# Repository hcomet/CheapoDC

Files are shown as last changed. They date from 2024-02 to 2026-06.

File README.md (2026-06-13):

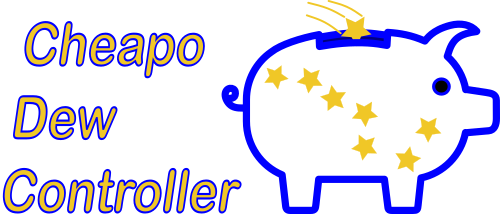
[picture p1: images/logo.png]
CheapoDC Logo
# 

# Introducing CheapoDC

The Cheapo Dew Controller, or CheapoDC, is a low cost, easy to build DIY dew controller based on an ESP32-C3 mini.
Parts required include the ESP32-C3 mini, a MOSFET module for each output, a 12V to 5V buck converter, some protoboard,
 RCA sockets, a 12V barrel socket and wire. Cost of the parts should be less than $20 for a unit that
controls 2 dew heater straps.

A primary goal was to keep the project cheap, simple and easy with:

* minimal low cost off the shelf components
* no coding or Arduino IDE experience necessary with both [WebFlash](https://hcomet.github.io/CheapoDC/CheapoDCFlash.html) and [HTTP OTA Update](https://hcomet.github.io/CheapoDC/CheapoDCWebUpdate.html) support
* Comprehensive [Web UI](#web-ui) for configuration and management
* [INDI](https://www.indilib.org/) and [StellarMate](https://stellarmate.com/) support 'out-of-the-box'

CheapoDC can select from four weather sources to provide the local temperature and humidity. 
* The first two, **OpenWeather** and **Open-Meteo**, leverage the ESP32 WiFi
capability to query one of the two open weather service APIs. Either the [OpenWeather](https://openweathermap.org/) API
or the [Open-Meteo](https://open-meteo.com/) API may be used to retrieve ambient temperature, humidity and dew point
for the controller's geographic location. No additional
components, such as temperature or humidity probes, are required with these weather sources. 
* The third weather source option, **External Source**, allows weather information to be pushed to the CheapoDC via the API. A personal weather station may be leveraged for local weather data using this option.
* The fourth option, **Internal Source**, requires an optional Humidity Sensor be added to the CheapoDC to provide required weather data.

The CheapoDC may be set up using a basic configuration with two dew strap outputs or it may be configured with up to
four additional outputs or the optional humidity sensor. Each CheapoDC Output is controlled by a separate MOSFET module tied to one of the ESP32
GPIO pins. The four additional outputs may be configured to be managed either automatically using the CheapoDC dew
control algorithm, along with the two main dew controller outputs,
or manually via the Web UI or API. Dew control algorithm managed pins and thus dew strap outputs are all tied to the
same ESP32 PWM channel and will have the same output.

CheapoDC hardware details can be found in the [Hardware](#hardware) section of this document.

CheapoDC firmware installation details may be found with the source code in the [CheapoDC/README.md](./CheapoDC/README.md#installing-cheapodc). Installation may be done by:

* Using WebFlash, a web-based utility that allows for the installation of the latest firmware directly to your ESP32-C3 based device.
* Building it yourself with the Arduino IDE.

CheapoDC also supports web-based Over-the-air (OTA) upgrades of the firmware using the CheapoDC Web UI.

# How the Dew Control Algorithm Works

When working in Automated mode, the controller will periodically calculate the power output to the dew straps using the
calculations below. The default output calculation or update period is 1 minute.

## Controller Power Output Calculation

### Variables

* **Set Point** = ***SP***
  * as set using the **Set Point Mode** selection.
* **Reference Temperature** = ***RT***
  * as set using the **Temperature Mode** selection.
* **Track Point** = ***TP***
  * the calculated temperature point where the **Tracking Range** starts. A **Reference Temperature** less than or equal
to the **Track Point** will cause the controller to use **Maximum Output**.
* **Track Point Offset** = ***TPO***
  * a temperature offset applied to the **Set Point** when calculating the **Track Point** relative to the **Set Point**.
The **Track Point Offset** may be set from -5.0&deg;C to 5.0&deg;C. The default is 0.0&deg;C.
* **Tracking Range** = ***TR***
  * the temperature range starting at the **Track Point** where the controller output ramps up from **Minimum Output** at the high end of the range to **Maximum Output** at the low end of the range. The range may be set to values from 4.0&deg;C to 10.0&deg;C. The default is 4.0&deg;C.
* **Power Output** = ***PO***
  * the percentage of power the controller is outputting to the dew straps. It varies from the **Minimum Output** setting to the **Maximum Output** setting.
* **Minimum Output** = ***MinO***
  * the minimum percent power setting for the controller to output when not in the **Off** **Controller Mode**. Defaults to 0%.
* **Maximum Output** = ***MaxO***
  * the maximum percent power setting for the controller to output when at full output. Defaults to 100%.

### Calculations

$`TP = SP + TPO`$

$`IF`$ $`(RT <= TP )`$ $`THEN`$ $`PO= MaxO`$

$`IF`$ $`(RT >= (TP + TR))`$ $`THEN`$ $`PO = MinO`$

$`IF`$ $`(RT <(TP + TR))`$ $`THEN`$ $`PO = MinO + (MaxO - MinO) * ( 1 - ((RT - TP)/TR))`$

### Examples

Example 1 is primarily a reference image to illustrate the variables defined above.

* Power Output curve is shown relative to the Track Point and the Tracking Range. While the Reference Temperature is greater than the high end of the Tracking Range the Power Output is set to Minimum Output. The Power Output ramps up linearly through the Tracking Range from the Minimum Output to the Maximum Output as the Reference Temperature drops.
* This example shows a Reference Temperature, RT = 8°C, which is greater than the upper end of the Tracking Range, causing Power Output to be set to Minimum Output. In this case Minimum Output is set to 10%.
* The upper end of the Tracking Range, at 7°C, is determined from the Set Point (SP = -2°C) plus the Track Point Offset (TPO = 4°C), creating a Tack Point, TP = 2°C, plus the Tracking Range (TR = 5°C).  

   **NOTE:** The Set Point and the Reference Temperature values may vary from one output calculation to the next with each weather update.

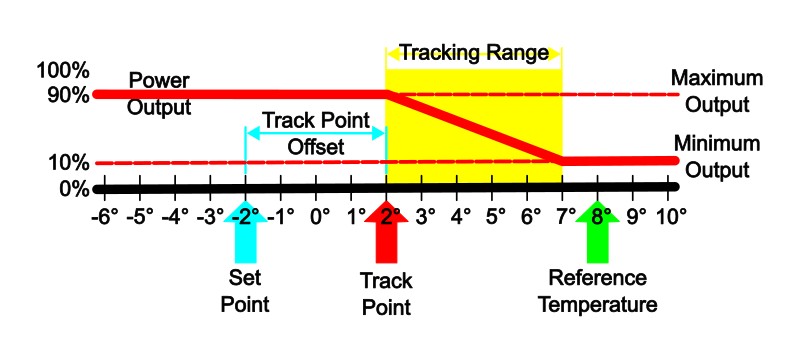
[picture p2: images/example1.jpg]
Example 1


Example 2 shows changing the values of the controller configuration variables can affect the Power Output calculation.

* The Set Point, SP = -2°C, and the Reference Temperature, RT = 8°C, the same as in Example 1. However, changing the Track Point Offset, now TPO = 2°C, and the Tracking Range, now TR = 10°C, has changed the Power Output as well as flattening the Power Output curve.
* The Maximum Output has been increased, MaxO = 100%, to allow full power output to be reached at 0&deg;C.

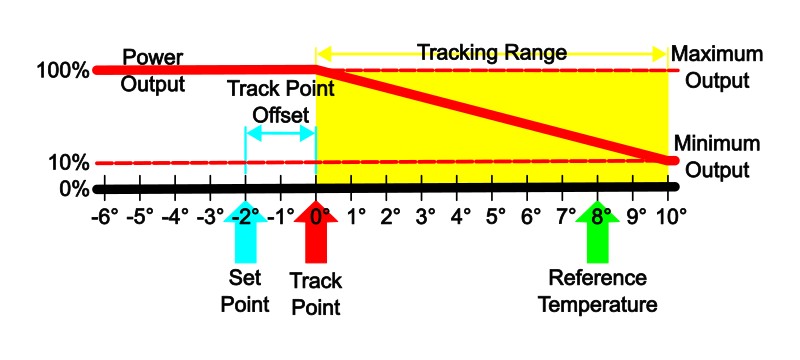
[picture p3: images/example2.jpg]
Example 2


## Dew Controller Configuration Settings

The following modes of operation are used by CheapoDC to determine overall controller operation as well as which values to assign to the Set Point and Reference Temperature when calculating output.

### Controller Mode

The Controller Mode selects the overall operating mode of the dew controller.

#### Automatic

* Uses the **Set Point Mode** and **Temperature Mode** settings to calculate the controller output based on the Power Output calculations above. In Automatic mode the Power Output calculation will be run periodically based on the Update Output Every setting. This may be set to a value from 1 to 20 minutes. The default is 1 minute. Automatic mode may be used with or without internet access.

#### Manual

* Controller output is manually controlled by setting the **Dew Controller Output** either through the Web UI or the API. When in Manual mode the periodic Power Output calculation is suspended. Using Manual control is an option if internet access for OpenWeather API queries is not available.

#### Off

* Controller output is set to Zero.

### Set Point Mode

The Set Point Mode selects what will be used as the SetPoint for calculating Power Output.

#### Dew Point

* Uses the **Dew Point** as the Set Point used for calculating output. This is the default selection.

#### Temperature

* Uses a **Temperature Set Point** value input via the Web UI or API as the Set Point for calculating output. If the CheapoDC is being used without internet access, then this mode allows a Set Point to be defined when the Dew Point cannot be determined through the OpenWeather API.

#### Midpoint

* Uses the midpoint between the current **Temperature Mode** temperature value and the Dew Point value as the Set Point for calculating output. The impact of selecting this mode is to effectively double the Tracking Range and further flatten the ramp of the Power Output curve.

### Temperature Mode

The Temperature Mode selects how the Reference Temperature will be determined for calculating the Power Output.

#### Weather Source

* Uses the Ambient Temperature returned by the selected Weather Source. This is then used as the Reference Temperature for calculating the controller output.

#### External Input

* Use the **External Input** temperature set through the [Web UI](#cheapodc-controller-configuration) or [API](#cheapodc-api) as the reference temperature for calculating the controller output. This may be the preferred mode when using the controller with KStars/Indi. The CheapoDC [Indilib driver](#indi-driver) can use a temperature probe attached to a focuser as the external input.  
<br>**NOTE:** If no temperature values have been set for External Input, then a value of **-127.0°C** will be shown. The Controller, when in Automatic Mode with Temperature Mode set to External Input,  will set output power at the configured minimum output until a value is set via the WebUI or API.

## Hardware

One of the goals with the CheapoDC is for it to be relatively easy to assemble. Although some soldering will be
required the number of connections is minimized by using common modules. This section focuses on what is required
to build a basic two dew strap controller commonly needed for a primary telescope and secondary guide scope.

If you need additional dew controller outputs or the ability remotely control the power to another device then that
information is covered [here](https://hcomet.github.io/CheapoDC/CheapoDCBuild.html).

If you are looking to add the optional SHT30 Humidity sensor to support a complete standalone device, that information is covered [here](https://hcomet.github.io/CheapoDC/CheapoDCSensor.html).

### Component list

* ESP32-C3 SuperMini (Other ESP32 modules should work but this one is very small and low priced) Example: [https://www.aliexpress.com/item/1005005967641936.html?spm=a2g0o.order_list.order_list_main.10.3b2c1802dRy3Tw](https://www.aliexpress.com/item/1005005967641936.html?spm=a2g0o.order_list.order_list_main.10.3b2c1802dRy3Tw)
* Buck converter to reduce 12V to 5V. I used an [LM2596 Module](https://www.amazon.ca/dp/B08Q2YKJ6Q?psc=1&ref=ppx_yo2ov_dt_b_product_details). You could also use an [MP1584EN Module](https://www.amazon.ca/eBoot-MP1584EN-Converter-Adjustable-Module/dp/B01MQGMOKI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). These modules often have an adjustable output. You'll need to use a Voltmeter to adjust the output to 5 volts before hooking it up.
* Two [dual-MOSFET Modules](https://www.amazon.ca/dp/B08ZNDG6RY?psc=1&ref=ppx_yo2ov_dt_b_product_details) to handle output to the dew straps while being able to be triggered by the 3.3V levels from the ESP32 PWM pins.
* A resettable fuse that can handle 5A. An example [5A PPTC](https://www.amazon.ca/10pcs-5000MA-Resettable-RGEF500-GF500/dp/B092T9Q3QR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)
* Optionally an LED and resistor for the status LED. Many astrophotographers do not want power LEDs or lights of any sort on their equipment. If you fall into this category, then just use the ESP32 onboard LED as the status LED. If you would prefer a visible status LED on your project case, then you may optionally add one. Status LED details may be found in the [Status LED Section](#cheapodc-status-led).  
In my implementation I used a red LED connected to the same pin as the onboard LED, pin 8. I used a 1K resistor to keep the LED fairly dim while still working.
* Some assorted hardware:
  * 12VDC 5.5mm x 2.1mm socket. Common socket size used for Astronomy.
  * Switch that will work for 12VDC at 5A.
  * Two RCA sockets. RCA plugs are commonly used for dew straps.

### Basic Wiring Diagram

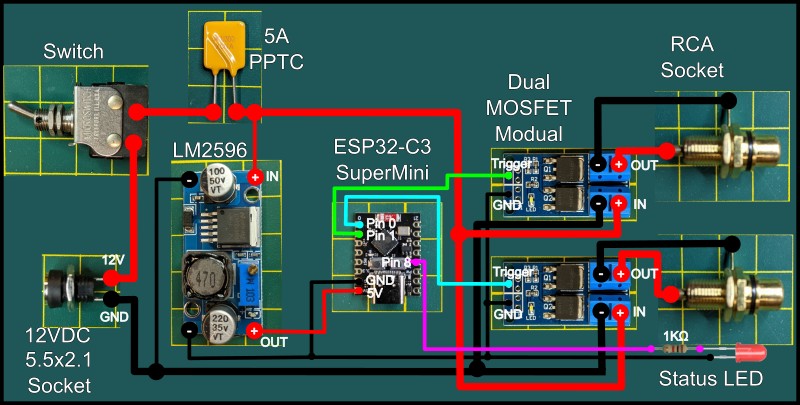
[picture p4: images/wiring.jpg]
Wiring Diagram


The default configuration for the basic dual output controller uses Controller Outputs, 0 and 1, mapped to GPIO pins 0 and 1.
If you cannot use these GPIO pins, then they may be changed using the Web UI on the [Device Management](#cheapodc-device-management)
page or the default values may be changed in the [CDCDefines.h](CheapoDC/README.md#configure-firmware-in-the-cdcdefinesh-file) file
before building the firmware.

### Working Implementation

Assembled in a 6 inch piece of 2"x1" aluminum channel. This also has Pin 8, which is the status LED, connected to an extra LED on the left side for external visibility. The ESP32-C3 is also mounted in some protoboard to make the wiring easier. If you plan to use a small case like this, use silicone hookup wire. The extra flexibility of silicone wire will save a lot of frustration. I used 22 awg wire for the 5V and 3.3V ESP32 connections and 18 awg wire for the 12V connections.

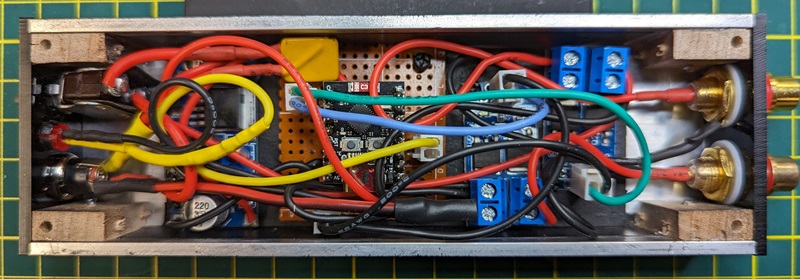
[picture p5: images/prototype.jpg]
Working Prototype


Two completed CheapoDCs from the outside.

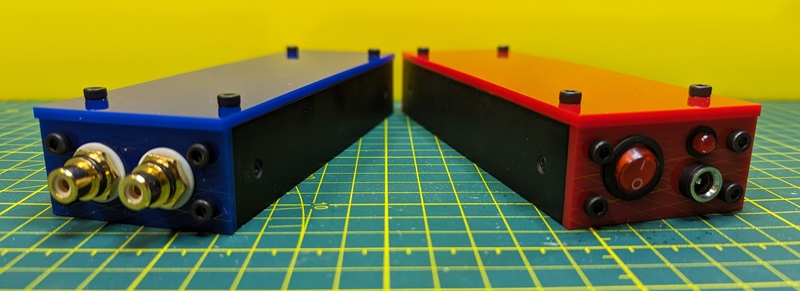
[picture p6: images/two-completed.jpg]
Two completed


## Firmware

How to build the CheapoDC firmware can be found [here](/CheapoDC/README.md). All aspects of the CheapoDC are configurable through the [WebUI](#web-ui) making [WebFlash](https://hcomet.github.io/CheapoDC/CheapoDCFlash.html) the easiest way to install and then configure firmware.

## Weather Source

CheapoDC requires temperature and humidity information to calculate the dew point and then the required controller output power for dew prevention. This information is provided by a Weather Source. CheapoDC can query one of two open weather API services, be provided weather information via the CheapoDC API or use an optional internal humidity sensor. The Weather Source may be set using the [Web UI](#cheapodc-controller-configuration) or through the [API](#cheapodc-api). The following four Weather Sources are available:

### [Open-Meteo](https://open-meteo.com/) (Default)

pen-Meteo, an open API based weather service, is the default Weather Source for CheapoDC. Use of the Open-Meteo API does not require any registration for current weather queries. The free level allows for 10,000 API calls per day. Weather updates seem to be regular at a 15 minute interval. While using a 5 minute query interval, several CheapoDCs can be running at the same time without issue. Requires correct location information and internet access to work.

### [OpenWeather](https://openweathermap.org/)

 OpenWeather, also an API based weather service, requires a registered account and API key. The account is free and allows for up to 60 queries/minute and 1,000,000 per month. Weather updates can occur from 5 to 20 minutes apart. Doing an API call every 5 minutes is more than adequate for dew control and even with 2 or 3 CheapoDC's sharing a key should have no issue at the free account level. Register and get your API key [here](https://home.openweathermap.org/users/sign_up). Requires correct location information and internet access to work.

### External Source

 When the Weather Source is set to External Source the temperature and humidity values for your location must be set via the CheapoDC API. This allows for integration with other weather services or personal weather stations. The [INDI driver](#indi-driver) supports this capability.

 ### Internal Source

 When the Weather Source is set to Internal Source the temperature and humidity values for your location are retrieved from an SHT3x series humidity sensor. The sensor must be connected to the ESP32 C3 and configured on the [Device Management](#cheapodc-device-management) page of the WebUI.

### Which Open Weather Service to use?

Both services require a location using Latitude and Longitude which you can set using the CheapoDC [Web UI](/README.md#web-ui) or [CheapoDC API](#cheapodc-api). Both sources will use weather stations close to the provided coordinates. OpenWeather provides the name of the weather station used in its response. Open-Meteo does not. If run side-by-side with the same co-ordinates they provide slightly different results. You may want to check which service provides the best results for your location.

As indicated the default service is Open-Meteo. This is primarily because no registration is required to use the open service.

## Web UI

CheapoDC comes with a Web UI that supports basic web authentication. The default is "admin" for both username and password. The password can (and should) be changed on the WebUI [Device Management](#cheapodc-device-management) page. TLS (or HTTPS) is not supported. Security is minimal with the intention to provide a deterrent to someone easily doing an OTA upgrade to the firmware or uploading files to the LittleFS partition.

The Web UI has 4 main pages, a dashboard, a configuration page, a device management page and a file management page.

### CheapoDC Dashboard

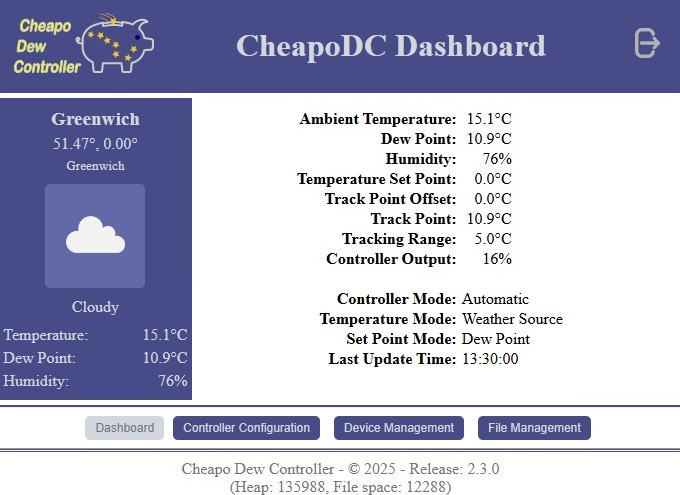
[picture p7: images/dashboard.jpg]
CheapoDC Dashboard
  

The Dashboard provides a summary of the current location, weather, controller output and settings. Internet connectivity is required for current weather information and the weather icon.

### CheapoDC Controller Configuration

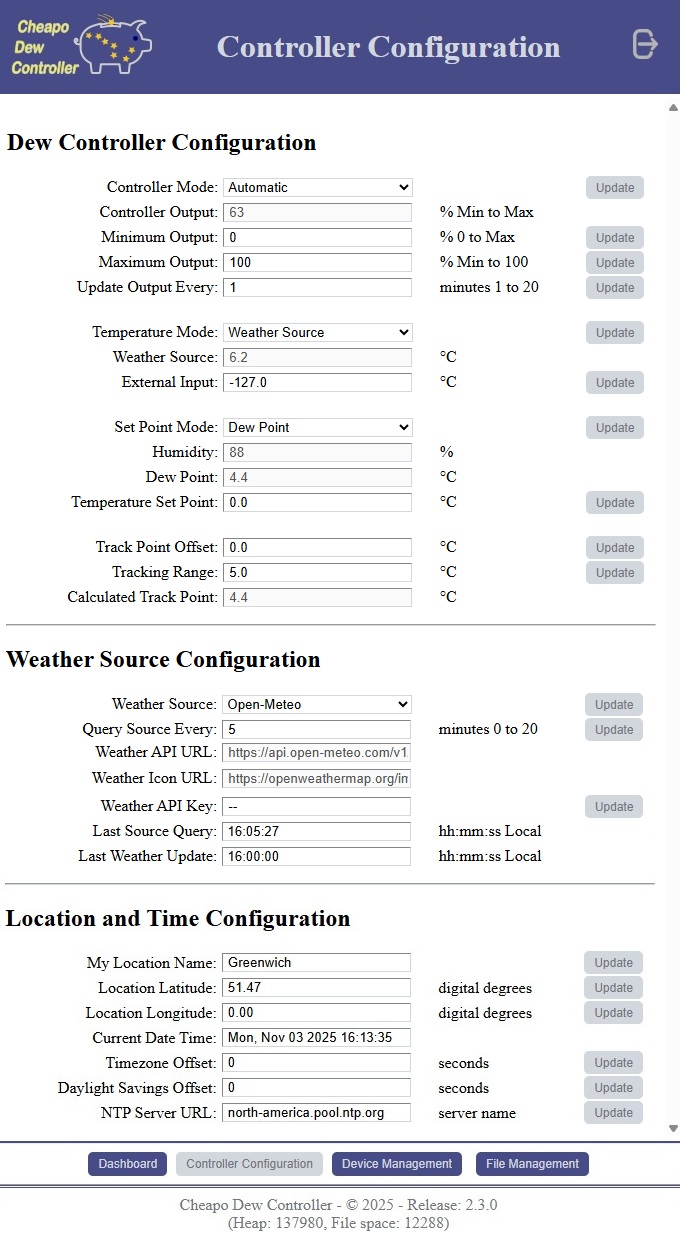
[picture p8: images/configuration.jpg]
CheapoDC Configuration
  

CheapoDC Configuration page is where dew controller parameters may be set. These include the [Controller Mode](#controller-mode), [Temperature Mode](#temperature-mode), [Set Point Mode](#set-point-mode), [Weather Source](#weather-source-1) and [variables](#variables) that affect dew controller output.

The Location and Time Zone may be set here and are required for proper operation when using either Open-Meteo or OpenWeather as a Weather Source.

### CheapoDC Device Management

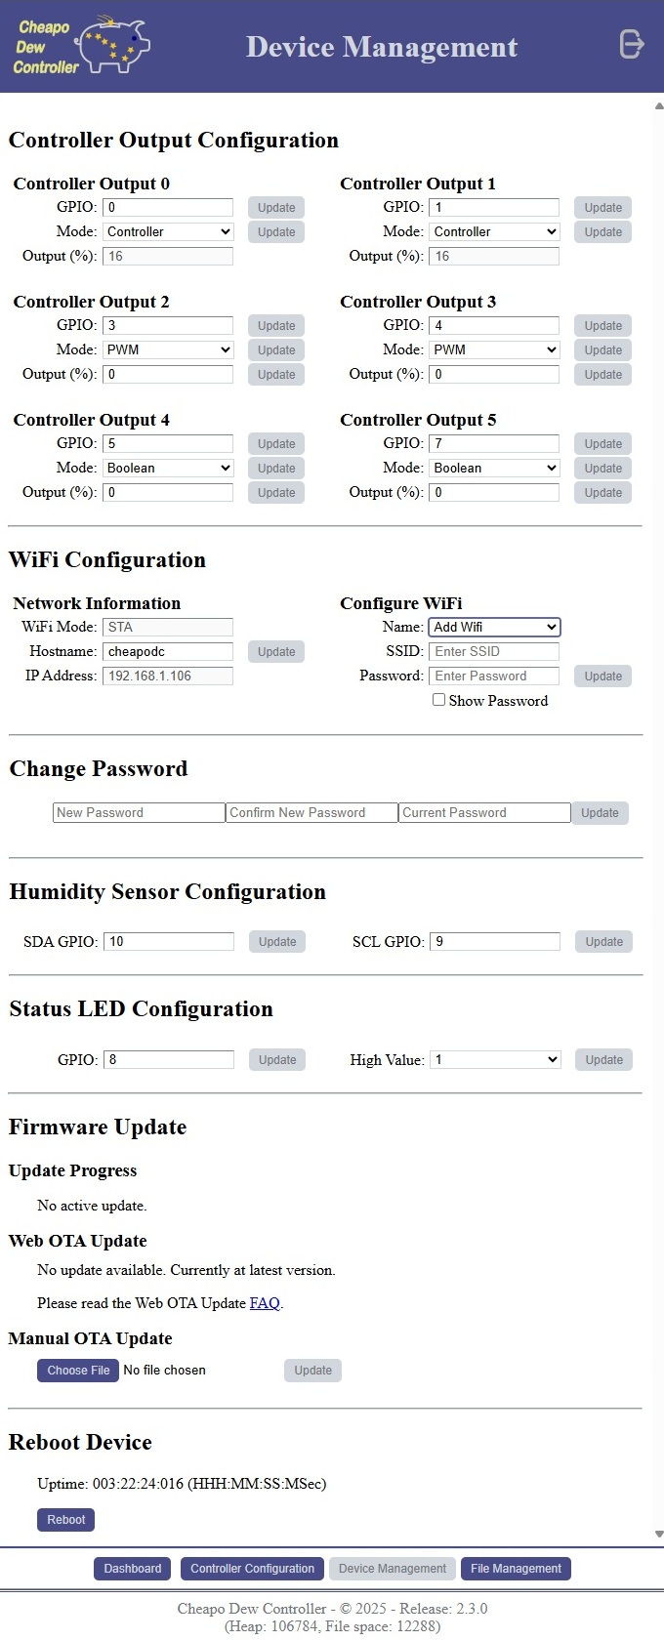
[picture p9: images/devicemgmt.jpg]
CheapoDC Device Management
  

The Device Management page is where device level configuration is done for the CheapoDC. This includes:

#### Controller Output Configuration

Used to configure GPIO Pin mappings for outputs as well as setting the Output Mode for each output. The CheapoDC can support up to 6 Controller Output Pins, Pin 0 through Pin 5. Pins 0 and 1 may only be used as dew controller outputs while Pins 2 through 5 may be set to any of the supported Output Modes:

##### Output Modes

|Output Mode|Description|Supported Output Pins|
|---|---|---|
|Disabled|Output is disabled. The default. GPIO pin mapping set to -1.|Pin 0 through Pin 5|
|Controller|Output is controlled by the dew controller.|Pin 0 through Pin 5|
|PWM|Output is manually controlled using PWM and output may be set from 0% to 100%.|Pin 2 through Pin 5|
|Boolean|Output is manually controlled and may be either Off (0%) or On (100%).|Pin 2 through Pin 5|

Note that a Controller Output Pin to GPIO Pin mapping must be set before an Output Mode may be selected. These settings may be controlled via the Web UI or the API.

#### WiFi Configuration

Shows current network information and allows you to configure the hostname and WiFi access point to use for network access. CheapoDC can be configured to step through multiple access points to make a WiFi connection.

* Network Information
  * WiFi Mode: STA = Station Mode, AP = Access Point Mode.
  * Hostname: Current active hostname. If updated a reboot is required to see the new hostname.  
  **Note:** Changing the hostname will also change the SSID for the device when in Access Point Mode.
  * IP Address.
* Configure WiFi
  * Name: Allows you to pick an access point for editing the password. Or select `Add WiFi` to add an access point.
  * SSID: Is the access point SSID point to add or edit. To delete an access point, blank out the SSID and click **Update**.
  * Password: Is the password for the access point. **Show Password** will only work for adding a new WiFi access point.

Changes to any of the WiFi Configuration setting require a reboot to take effect.

#### Change Password

Changing the default password of ***admin*** to your own password is recommended.

#### Humidity Sensor Configuration

Used to configure which pins are used for by the SHT3x humidity sensor. The humidity sensor uses the I2C protocol and two GPIO pins are required. One for the I2C SDA (data) line and one for the I2C SCL (clock) line. If using the humidity sensor, then it's recommended to use pin 10 for SDA GPIO and pin 9 for SCL GPIO. If not using the humidity sensor, then leave the two values set to -1. If either setting has a negative value, then the firmware will not attempt to initialize I2C and the humidity sensor.

#### Status LED Configuration

Used to change the Status LED pin mapping from the default of GPIO 8. Also used to set the active High Value to ***1*** or ***0***.

#### Firmware Update

CheapoDC supports two methods for updating firmware.

1. Web OTA Update: Will indicate when a new release is available and then allow for an HTTP based OTA update. This will update both the firmware and data partitions while preserving your configuration settings. No software or Arduino IDE knowledge is required for this update method. Please consult the [Web OTA Update FAQ](https://hcomet.github.io/CheapoDC/CheapoDCWebUpdate.html) for details.
2. Manual OTA Update: Allows for an OTA update to firmware that has been compiled and built on your own machine. This only updates the data partition. You will need to manually update the files in the data partition using the [File Management UI](#cheapodc-file-management). At least Arduino IDE knowledge is required for this method.

#### Reboot Device

To remotely reboot the CheapoDC.

### CheapoDC File Management

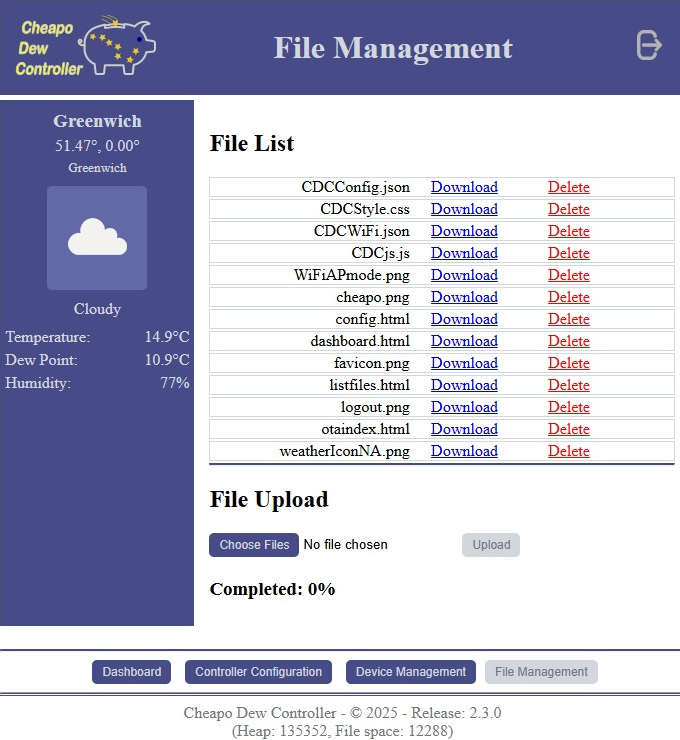
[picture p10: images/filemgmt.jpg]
  

The CheapoDC uses LittleFS for file storage on the ESP32. Although LittleFS supports directories as well as files CheapoDC uses a flat structure and all files are managed at the root. The file management page supports upload, download and delete functions.

## CheapoDC Status LED

The Status LED is used to provide information about the current status of the CheapoDC. Status blinking lasts for 10 seconds. It will blink as WiFi access attempts are made. If a Station mode connection is successfully made to an access point, then the status LED will slow blink (1 second cycle). If no connection is made, then the CheapoDC will go into Access Point mode. The status LED will then fast blink (200ms cycle).

The status LED will also blink for 10 seconds after the controller changes the power output and after an API or Web UI driven controller configuration change.

If the status LED is not turning off after connecting to WiFI or after the 10 second blink, then you may need to reverse the High value setting. This can also be done in the Web UI by changing the High Value setting in [Status LED Configuration](#status-led-configuration).

## CheapoDC API

The CheapoDC provides API access to all configuration and data items available through the [Web UI](/README.md#web-ui). There is no authentication support in the API, but the API also does not support firmware OTA updates or file management. These can only be done through the Web UI.

CheapoDC supports two API mechanisms:

1. TCP API using JSON syntax
2. Basic Web API utilizing HTTP POST

The APIs use the same commands which are listed in the top of [CDCommands.cpp](/CheapoDC/CDCommands.cpp). Commands are 2 to 4 character strings. For each command there is a map indicating:

* the number of the command,
* whether or not the value associated with the command is to be saved or loaded using the CDCConfig.json file,
* units used for the value. Units are HTML or JSON formatted and may be:
  * None: empty string.
  * Degrees Celsius: "\&deg;C"
  * Decimal Degrees: "\&deg;"
  * Percent: "\&percnt;"
  * Milliseconds: "msec"
  * Seconds: "sec"
  * Minutes: "min"
  * JSON ENUM, for enumerated values like Controller Mode.
    * ie: "{"Mode":["Automatic","Manual","Off"]}"

The table below provides a list of the commands, but the code is the final correct source of truth here.

* String maximum lengths are identified in the table.
* Floats are truncated to 2 decimal places.
* All commands except **QN** and **PWDH** support getter API methods.
* For security reasons, **PWDH** does not allow a getter API but it also restricts the setter to the Web API and HTTP POST method. It also requires that the current Password digest hash be submitted as a second parameter.
* The **QN** command is a setter only command. It requires a value that is not Null. "NA" works.
* Commands supporting a **Setter** method are identified.
* The **ATPQ** and **HU** commands are only setter commands when Weather Source is set to External Source.
* Date and time responses are in local time based on the Time Zone Offset and DST Offset values.
* Controller Output commands: CPP#, CPM# and CPO# are independent API commands where the # must be one of 0, 1, 2, 3, 4 or 5.
* Controller Output command CPP# allows a Controller Output to be mapped to -1 for Disabled or GPIO 0 through 39. Which actual GPIO pin to choose is ESP32 module dependent.
* Using an invalid command or trying a setter on a command not supporting a setter will return an error.
* Strictly speaking command values are always treated as Strings since the values are always enclosed in quotes in the JSON. Conversion to appropriate type is handled internally.
* The **CLC** command has been deprecated.

### CheapoDC Commands

|Command|Setter|Units|Type|Description|
|:---:|:---:|-----|----|---|
| TMFL |&cross;|  HTML | String [*] | File list in HTML for use in Web UI |
| WICON  |&cross;|  None | String [4] | Weather Icon for use with OpenWeather |
| WDESC  |&cross;|  None | String [32]| Weather description |
| ATPQ |&check;|  &deg;C | Float | Ambient temperature from weather query<br>Settable when Weather Source is set to External Source |
| HU |&check;|  &percnt; | Integer | Relative humidity (0 to 100)<br>Settable when Weather Source is set to External Source. |
| DP |&cross;|  &deg;C | Float | Dew point|
| SP |&check;|  &deg;C | Float | Temperature set point|
| TPO |&check;|  &deg;C | Float | Track Point offset (-5.0 to 5.0)|
| TKR |&check;|  &deg;C | Float | Tracking range (4.0 to 10.0)|
| DCO |&check;|  &percnt; | Float | Dew Controller Output (0 to 100)<br>Settable when Dew Controller Mode set to Manual. |
| WS |&check;|  None | ENUM | Weather source <br>Open-Meteo = 0<br>OpenWeather = 1<br>External Source = 2<br>Internal Source = 3|
| LQT |&cross;|  None | String [32] | Last weather query time|
| LQD |&cross;|  None | String [32] | Last weather query date|
| QN |&check;|  None | String [4] | Query weather now (Set only command)|
| FW |&cross;|  None | String [16] | firmware version|
| HP |&cross;|  Bytes | Integer | Heap size|
| LFS |&cross;|  Bytes | Integer | LittleFS remaining space|
| DCM |&check;| Enum | Enum | Dew controller mode<br>Automatic = 0<br>Manual = 1<br>Off = 2|
| DCTM |&check;| Enum | Enum | Dew controller temperature mode<br>Weather Source = 0<br>External Input = 1 |
| SPM |&check;| Enum | Enum | Dew controller set point mode<br>Dew Point = 0<br>Temperature = 1<br>Midpoint = 2 |
| WQE |&check;|  Minutes | Integer | Weather query every|
| UOE |&check;|  Minutes | Integer | update output every|
| WAPI |&cross;|  None | String [256] | Weather API URL|
| WIURL  |&cross;|  None | String [256] | Weather Icon URL|
| WKEY |&check;|  None | String [64] | Weather API Key|
| LAT |&check;|  &deg; (Digital) | Float | Location latitude (-90.00 to 90.00)|
| LON |&check;|  &deg; (Digital) | Float | Location longitude (-180.00 to 180.00)|
| LNM |&check;|  None | String [32] | Location name|
| TMZ |&check;|  Seconds | Integer | Location time zone (seconds)|
| DST |&check;|  Seconds | Integer | Location DST offset (seconds)|
| LED |&check;|  None | Integer | Status LED GPIO pin|
|LEDH|&check;|None|Integer|Status LED High value.<br>1 or 0.|
| NTP |&check;|  None | String [64] | NTP serverName|
| OMIN |&check;|  &percnt; | Integer | DC Min output (0 to Max-1)|
| OMAX |&check;|  &percnt; | Integer | DC Max output (Min+1 to 100)|
| CDT |&cross;|  None | String [64] | Current Date Time|
| ATPX |&check;|  &deg;C | Float | External Temperature input by external app|
| CTP |&cross;|  &deg;C | Float | Current Track Point Temperature|
| WUL |&cross;|  None | String [32] | Weather station reported in query|
|  ~~CLC~~ |&cross;|  &percnt; | ~~Integer~~ | ***Deprecated***|
| LWUT |&cross;| None | String [32] | Last weather update time<br>hh:mm:ss|
| LWUD |&cross;|  None  | String [32] | Last weather update date<br>DDD, dd MMM yyyy|
| UPT |&cross;|  None | Integer | Device uptime<br>hhh:mm:ss:msec|
| WIFI |&cross;|  None | String [4] | WIFI mode AP (Access Point) or STA (Station Mode)|
| IP |&cross;|  None | String [16] | IP Address|
| HN |&cross;|  None | String [16] | Host name |
| WQEN |&check;|  None | Bool | Web Query Enabled<br>False = 0<br>True = 1|
| CPP# |&check;|  None | Integer |Controller Output (0 to 5) to GPIO pin mapping<br>-1 to 39<br>-1 = Disabled|
| CPM# |&check;|  None | ENUM |Controller Output (2 to 5) Mode <br>Disabled = 0<br>Controller = 1<br>PWM = 2<br>Boolean = 3|
|CPO#|&check;|&percnt;|Integer|Controller Power Output (0 to 5), mode dependent:<br>Set - PWM, Boolean<br>Get - all modes|
|  SDAP  |&check;| None | Integer | Humidity sensor SDA GPIO mapping<br>-1 to 39<br>-1 = Disabled|
|  SCLP  |&check;| None | Integer | Humidity sensor SCL GPIO mapping<br>-1 to 39<br>-1 = Disabled|
|PWDH|&check;|None|String[32]|Change the [Digest access authentication](https://en.wikipedia.org/wiki/Digest_access_authentication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,It%20uses%20the%20HTTP%20protocol.) MD5 Password Hash. |
|FWUP|&cross;|None|String[16]|Returns new FW release availability:<br>x.y.z = update available<br>NOFWUPDATE = no update<br>NOSUPPORT = Web Update not supported|

### TCP API

The TCP API uses JSON formatted commands over TCP on port 58000. JSON strings must always be terminated with a newline character "\n". "cmd" in the following formats is the 2 to 4 character command identified in [CDCommands.cpp](/CheapoDC/CDCommands.cpp).

#### Setter format

* Send: **{"SET":{"cmd":"value"}}**
* Response: **{"RESULT": result}**  

#### Getter format

* Send: **{\"GET\":"cmd"}**
* Response: **{"cmd":"value"}** - *if successful*
* Response: **{"RESULT": result}** - *if failure*

***NOTE:*** Where a response of **{"RESULT": result}** is received ***result*** may be one of:  

| result  |  Reason |
|:---:|---|
|0|for success |
|-1|for a command execution error|
|-2| for an unknown command or API parsing error|

### Web API

The Web API uses POST and "x-www-form-urlencoded" with name value pairs.

#### Setter Format

* Send: **cmd=value**  
* Response: HTTP status code of 200 on success.

#### Getter Format

* Send: **get=cmd**  
* Response: **cmd=value**  
success has HTTP status code of 200.

## Configuration Files

See the Configuration Files section in [Building and Installing CheapoDC](./CheapoDC/README.md/#configuration-files).

## [INDI Driver](https://www.indilib.org/aux/cheapodc-dew-controller.html)

An INDI driver is now available in the master branch as of INDI release 2.0.7, April 1, 2024. Details should become available on the [INDI website devices list](https://www.indilib.org/aux/cheapodc-dew-controller.html) as well as the [StellarMate website devices list](https://www.stellarmate.com/devices.html).

Driver version 1.2 supports the latest versions of the CheapoDC firmware adding support for the four Additional Controller Outputs. Up to date driver documentation is maintained [here](https://hcomet.github.io/CheapoDC/indi/CheapoDC.html).

# Third Party Acknowledgements

* Two libraries are bundled into CheapoDC:
  * esp32FOTA from Chris Joyce provides the [Web OTA Update](https://hcomet.github.io/CheapoDC/CheapoDCWebUpdate.html) capability for HTTP OTA updates. The original library may be
  found at [https://github.com/chrisjoyce911/esp32FOTA](https://github.com/chrisjoyce911/esp32FOTA). esp32FOTA also bundles in a semantic version parsing library, [semver](https://github.com/h2non/semver.c), from h2non.
  * EasyLogger from Alex Skov Jensen provides the debug logging macros. The original library may be
  found at [https://github.com/x821938/EasyLogger](https://github.com/x821938/EasyLogger).
* Other libraries used by CheapoDC include:
  * [ArduinoJson by Benoit Blanchon](https://arduinojson.org/)
  * [ESP Async WebServer by ESP32Async](https://github.com/ESP32Async/ESPAsyncWebServer)
  * [Async TCP by ESP32Async](https://github.com/ESP32Async/AsyncTCP)
  * [Sensirion I²C SHT3X by Sensirion](https://github.com/Sensirion/arduino-i2c-sht3x)
  * [Sensirion Core by Sensirion](https://github.com/Sensirion/arduino-core/)
  * [Time by Michael Margolis](https://playground.arduino.cc/Code/Time/)
  * [ESP32CertBundle by TANAKA Masayuki](https://github.com/tanakamasayuki/ESP32CertBundle)  
* The [WebFlash](https://hcomet.github.io/CheapoDC/CheapoDCFlash.html) capability uses [ESP Web Tools](https://esphome.github.io/esp-web-tools/) from [Home Assistant](https://www.home-assistant.io/).

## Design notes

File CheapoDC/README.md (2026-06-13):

# Installing CheapoDC

## WebFlash, the Easy Option for New Devices

If you are using an [ESP32-C3 SuperMini](https://michiel.vanderwulp.be/domotica/Modules/ESP32-C3-SuperMini/) or any other ESP32-C3 module then the easiest way to load the CheapoDC firmware onto your device is to use [WebFlash](https://hcomet.github.io/CheapoDC/CheapoDCFlash.html). All necessary configuration changes may then be done through the [Web UI](../README.md#web-ui). 

You need to connect your ESP32-C3 to your computer via USB to use WebFlash. Go to the [WebFlash page](https://hcomet.github.io/CheapoDC/CheapoDCFlash.html) to install CheapoDC on your ESP32-C3. Then follow the instructions below in the [First Time Device Configuration](#first-time-device-configuration) section.

If you prefer to build the firmware yourself using the Arduino IDE, please continue to [Building and Installing CheapoDC](#building-and-installing-cheapodc)

## Upgrading from a Previous Release

There are four methods described below for upgrading CheapoDC firmware. Two leverage Over-the-air (OTA) update methods while the other two methods require a computer and USB connection to the device.

### 1. Web OTA Update

Introduced in the V2.2.0 release, [Web OTA Update](https://hcomet.github.io/CheapoDC/CheapoDCWebUpdate.html) is the simple and easy way to upgrade your CheapoDC firmware. When a new release is available it will be indicated in the **Web OTA Update**
section on the **Device Management** page of the CheapoDC WebUI. Just enter your CheapoDC password, click `Update` and the new release will be installed while preserving your CheapoDC configuration files.

>[!IMPORTANT]
> Due to a change to the issuing CA for GitHub Pages HTTPS certificates, Web OTA Update from V2.3.0 or earlier no longer works. V2.3.1 fixes the issue and Web OTA Update should work properly from that version onwards.
>
> Go to the section [***Web OTA Update Root CA Issue***](#web-ota-update-root-ca-issue) for details on how to get Web OTA Update to detect a new release and perform the firmware update from V2.2.0 or V2.3.0.

### 2. Manual OTA Update

Manual OTA Update allows you to do an OTA update using your own copy of the CheapoDC firmware binary image. Use the following steps:

1. Download the latest firmware release source code from <https://github.com/hcomet/CheapoDC/releases> and extract it to your local file system.
2. Get or generate the firmware binary image file by either:

   1. Downloading the latest CheapoDC binary image file from [https://hcomet.github.io/CheapoDC/firmware/CheapoDC.ESP32-C3.bin](https://hcomet.github.io/CheapoDC/firmware/CheapoDC.ESP32-C3.bin).
   2. Or generating the firmware binary image using the Arduino IDE and selecting `Sketch->Export Compiled Binary`. This will create a ***CheapoDC.ino.bin*** file under a ***build*** folder created in your sketch folder.  
   **Note:** Follow the instructions in [Build and Install the Firmware](#build-and-install-the-firmware) to set up the Arduino IDE for CheapoDC builds.

3. Use the **Manual OTA Update** `Choose File` in the Web UI to select the ***.bin*** file from step 2. Then click `Update` to flash the CheapoDC to the new version.
4. After the reboot, go to the [File Management](../README.md#cheapodc-file-management) page to upload the new release data files. Use `Choose Files` to browse to the ***CheapoDC/CheapoDC/data*** folder in the downloaded release from step 1. Then select all files **EXCEPT** the CDCWiFi.json file. Then click `Upload`.
5. Your upgrade should now be complete.

### 3. Upgrade using USB Connected Device and Arduino IDE

1. Preserve your current CheapoDC configuration and WiFi settings by first downloading the CDCConfig.json and CDCWiFi.json files
from your CheapoDC. This can be done using the Web UI from the [File Management](../README.md#cheapodc-file-management) page.
Place both files in the sketch data folder: ***CheapoDC/data***.
2. Build and upload the new firmware to your device.
   * If upgrading from a pre-V2.1.0 release, make sure to set *Erase All Flash Before Sketch Upload:* ***"Enabled"***  
   **NOTE:** Make sure to reset this to **"Disabled"** once you are done with the upgrade or the LittleFS partition will be erased with each
   firmware upload and you will need to upload your sketch data every time.
   * Make sure to have selected the *Minimal SPIFFS (1.9MB APP with OTA/190KB SPIFFS)* partition scheme.
3. Upload the files in the CheapoDC/data folder using the Sketch data uploading tool. Make sure to use an upload tool for the LittleFS filesystem.
4. Your upgrade should now be complete.

### 4. Upgrade using USB Connected Device and WebFlash

1. WebFlash will erase all flash memory on your CheapoDC. You must backup your current CheapoDC configuration and WiFi settings by first downloading the **CDCConfig.json** and **CDCWiFi.json** files
from your CheapoDC. This can be done using the Web UI from the [File Management](../README.md#cheapodc-file-management) page.
2. Use [WebFlash](https://hcomet.github.io/CheapoDC/CheapoDCFlash.html) to install the latest CheapoDC firmware onto your device.
3. Once the device has rebooted, it will be in access point mode. Use your computer to connect to the access point, SSID: cheapodc and Password: cheapodc.
4. Browse to the CheapoDC Web UI at [http://cheapodc.local](http://cheapodc.local) and login using the default userid and password: admin, admin.
5. Upload the previously backed up **CDCConfig.json** and **CDCWifi.json** files using the File Management page.
5. Goto to the Device Management page and reboot the device to complete the upgrade.

## Changes in CheapoDC V2

1. As of V2.2.0, CheapoDC now supports firmware and data partition upgrades using the Web UI and HTTP OTA. See the documentation on [Web OTA Update](https://hcomet.github.io/CheapoDC/CheapoDCWebUpdate.html) for details.
2. V2 contains changes to support new library versions:
   * Arduino core for ESP32 version 3.x support. Core Version 2.x support now deprecated as of CheapoDC V2.1.0.
   * Switch to the [ESP32 Asynchronous Networking Organization](https://github.com/ESP32Async) versions of
   ESPAsyncWebServer and AsyncTCP.
   * ArduinoJson version 7.x.
3. New libraries required in V2:
   * As of V2.3.0, [Sensirion Core by Sensirion](https://github.com/Sensirion/arduino-core/) and [Sensirion I²C SHT3X by Sensirion](https://github.com/Sensirion/arduino-i2c-sht3x) are required for humidity sensor support.
   * As of V2.3.1, [ESP32CertBundle](https://github.com/tanakamasayuki/ESP32CertBundle) is required to support [Web OTA Update](https://hcomet.github.io/CheapoDC/CheapoDCWebUpdate.html).
4. The following libraries are no longer required:
   * EasyLogger - a fixed copy of this library is included in the CheapoDC source to remove a macro definition conflict with ArduinoJSON.
   * ESP32Time.
5. As of V2.2.0, all major items that were previously required to be configured at compile time can now be configured through the Web UI or API at runtime. This includes:
   * [WiFi Configuration](../README.md#wifi-configuration): WiFi SSID and password can be set on the Device Management page.
   * Weather Source: The Weather Source may now be set through the Web UI or API. Open-Meteo is now the default Weather Source.
   * [Output to GPIO Pin mapping](../README.md#controller-output-configuration). All controller outputs may be configured using the Web UI or API. This includes the original two core dew controller outputs as well as the four new additional outputs added in V2.2.0.
   * [Status LED GPIO Pin](../README.md#status-led-configuration). The pin used for the status LED as well as whether it is active High or Low may be configured through the Web UI or API.
   * [Change Password](../README.md#change-password). The user Id remains **admin** but the password may now be changed in the Web UI. Password security has been improved by moving to using a [Digest access authentication](https://en.wikipedia.org/wiki/Digest_access_authentication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,It%20uses%20the%20HTTP%20protocol.) MD5 Password Hash.
6. New Weather Sources added for more flexibility and autonomous operation:
   * V2.2.0 added support for integration with personal weather stations or other weather services. When the Weather Source is set to ***External Source*** the local ambient temperature and humidity may be set through the API. The Dew Point and dew controller power output will then be calculated based on these externally set values.
   * V2.3.0 added support for connecting an SHT3x humidity/temperature sensor. When the Weather Source is set to ***Internal Source***, local ambient temperature and humidity will be taken from a temperature/humidity sensor connected to the CheapoDC. The SHT3x must be properly [connected and configured](https://hcomet.github.io/CheapoDC/CheapoDCSensor.html) for ***Internal Source*** to work.
7. API changes:
   * ***`CPPx`***, ***`CPMx`*** and ***`CPOx`*** API commands added to allow outputs **x = 0 to 5** to be configured for GPIO Pin mapping, Output Mode and Output Power respectively.
   * The ***`LED`*** API command changed to set the GPIO pin for the Status LED while ***`LEDH`*** sets the value of High to 1 or 0.
   * The Weather Source (***`WS`***) API command now supports a SET capability. This API command has also been changed
   to use an integer value to specify the Weather Source:  
   `[Open-Meteo = 0, OpenWeather = 1, External Source = 2, Internal Source = 3]`  
   External Source added in V2.2.0. Internal Source added in V2.3.0.
   * The Ambient Temperature from Weather Query (***`ATPQ`***) API command now supports a SET capability when the Weather Source is set to External Source.
   * The Humidity (***`HU`***) API command now supports a SET capability when the Weather Source is set to External Source.
   * ***`SDAP`*** and ***`SCLP`*** API commands added in V2.3.0 to allow for configuration of an internal humidity/temperature sensor. ***`SDAP`*** sets or gets the I2C SDA (data) pin. ***`SCLP`*** sets or gets the I2C SCL (clock) pin. Pins 10 and 9 are the recommended pins for SDA and SCL, respectively. A value of -1 (default) will disable the sensor. A reboot of the device is required for I2C changes to take effect.
   * The Weather API URL (***`WAPI`***) API command no longer supports a SET capability.
   * The Weather Icon URL (***`WIURL`***) API command no longer supports a SET capability.
   * The Cloud Coverage (***`CLC`***) API command has been deprecated.
8. Support for the Web Sockets based API has been deprecated and removed in V2.2.0. The TCP API continues to be supported and used by the INDI driver.
9. CheapoDC V2 will automatically upgrade the CDCConfig.json on your CheapoDC device when the new firmware version is installed. Previous configuration settings will be maintained. Follow the [Upgrade Steps](#upgrading-from-a-previous-release) below to preserve your
CheapoDC configuration files.
10. As of V2.3.0, when in Access Point Mode, CheapoDC will use the hostname for the SSID.
11. See the CheapoDC [release notes](https://github.com/hcomet/CheapoDC/releases) for additional details.

## Building and Installing CheapoDC

### Partition Scheme

The ESP32 Partition Scheme is a term used by the Arduino IDE to select a partition table that defines the flash memory organization and the different kinds of data that will be stored in each partition. The ESP32-C3, which this project uses, generally has 4MB of flash memory with the default partition scheme of *Default 4MB with spiffs (1.2MB APP/1.5MB SPIFFS)*.

The *Default 4MB with spiffs (1.2MB APP/1.5MB SPIFFS)* partition scheme provides two application partitions of 1.2MB to support OTA updates plus a 1.5MB SPIFFS partition used for LittleFS file storage. The latest version of CheapoDC using the latest Arduino library versions requires about 1.6MB of application space.

To allow for OTA updates, LittleFS storage and some expansion room for CheapoDC firmware the *Minimal SPIFFS (1.9MB APP with OTA/190KB SPIFFS)* partition scheme is used. Although this scheme provides enough application space it provides too little SPIFFS (data partition) space for the CheapoDC HTML, CSS and JS files without compression. The repository [**data source**](../data%20source/) folder contains he original source for these files. The repository [**CheapoDC/data**](../CheapoDC/data/) folder contains minified or compressed versions for installation in the LittleFS formatted data partition.

### Setting Up Your Build Environment

1. Install the Arduino IDE.  
  **NOTE:** Version 2.3.10 of the Arduino IDE is required. As of CheapoDC V2.3.1 verification of
  builds will only be done on IDE version 2.3.10 or newer.
2. Add support for ESP32 modules using the Boards Manager in the Arduino IDE.  
  **IMPORTANT:**
    * Install the boards plugin for ESP32 from Espressif Systems version 3.3.10 (Arduino core for the ESP32). CheapoDC V2.3.1 verification has been done with version 3.3.10.
    * CheapoDC is intended for use on ESP32 devices. The current version has been verified on an [ESP32-C3 SuperMini](https://michiel.vanderwulp.be/domotica/Modules/ESP32-C3-SuperMini/) board.
3. Install the ESP32 Sketch data uploader with support for LittleFS. The CheapoDC uses the LittleFS file system for configuration files and web pages uploaded from the ***CheapoDC/data*** folder. If the data is uploaded using any other file system format, such as SPIFFS, the CheapoDC firmware will not run properly.  
**NOTE:** The following link provides information on how to install a data uploader plugin with LittleFS support:
    * Arduino IDE 2.3.2+: [https://randomnerdtutorials.com/arduino-ide-2-install-esp32-littlefs/](https://randomnerdtutorials.com/arduino-ide-2-install-esp32-littlefs/)

4. Install the following libraries if not already installed:
   * [ArduinoJson by Benoit Blanchon](https://arduinojson.org/)  
     Version: 7.4.3
   * [ESP Async WebServer by ESP32Async](https://github.com/ESP32Async/ESPAsyncWebServer)  
     Version: 3.11.1
   * [Async TCP by ESP32Async](https://github.com/ESP32Async/AsyncTCP)  
     Version: 3.4.10
   * [Sensirion I²C SHT3X by Sensirion](https://github.com/Sensirion/arduino-i2c-sht3x)  
     Version 1.0.1
   * [Sensirion Core by Sensirion](https://github.com/Sensirion/arduino-core/)  
     Version 0.7.3
   * [Time by Michael Margolis](https://playground.arduino.cc/Code/Time/)  
     Version: 1.6.1
   * [ESP32CertBundle by TANAKA Masayuki](https://github.com/tanakamasayuki/ESP32CertBundle)  
     Version: 20260514.0.0

   **NOTES:**
   * Make sure that the only versions of **ESP Async WebServer** and **Async TCP** are the ones by ESP32Async. If you have other versions of the ESPSyncWebServer or AsyncTCP not from the links above they will need to be uninstalled to prevent issues with the build.
   * In general, if newer versions of a library are available then only use new subversions not new major versions. CheapoDC v2.3.1 was verified using the versions of libraries listed above.

5. Download the latest firmware release source code from <https://github.com/hcomet/CheapoDC/releases>  
  **NOTE:** After extracting the release to your filesystem open the ***CheapoDC.ino*** file in the Arduino IDE. This will open the full set of source files in the IDE.

>[!TIP]
>* Many ESP32-C3 board configurations (Dev Module, mini, super mini, micro etc..) have *USB CDC On BOOT:* ***"Disabled"***. This needs to be ***"ENABLED"*** or the Serial Monitor will not work.
>* CheapoDC uses *115200 baud* for the Serial Monitor Connection. Leave the default baud rate for the upload.
>* Its good practice to set *Erase All Flash Before Sketch Upload:* ***"Enabled"*** the first time you upload a new project to an ESP32. After that, make sure its set to ***"Disabled"*** to preserve the LittleFS partition content between uploads.

### Configure Firmware in the CDCdefines.h file

As of V2.2.0 changes to the ***CDCdefines.h*** file are **not** required since all key items can now be modified at runtime, via the [WebUI](../README.md#web-ui), and are saved to the [CDCConfig.json](#cdcconfigjson). If you do wish to configure/customize the firmware before building the following items may be modified in the ***CDCdefines.h*** file:

1. Set the default ESP32 GPIO pins to be used for Controller Outputs 0 & 1. ***DEFAULT: 0 & 1***.  
    ```#define CDC_DEFAULT_CONTROLLER_PIN0 0```  
    ```#define CDC_DEFAULT_CONTROLLER_PIN1 1```  
    *May be changed through the Web UI or API*
2. Set the PWM channel to use for Controller Outputs. ***DEFAULT: 0***.  
    ```#define CDC_CONTROLLER_PWM_CHANNEL 0```  
  **NOTE:** Changing this value may have a negative impact on CheapoDC operation. PWM channels 1 through 4 are reserved for the use of the additional Controller Outputs 2 through 5.
3. Set the pin for the status LED on you ESP32. ***DEFAULT: 8***.  
    ```#define CDC_DEFAULT_STATUS_LED_PIN 8```  
    *May be changed through the Web UI or API*  
    **NOTE:** Some ESP32-C3 modules have the Status LED wired so that setting the status pin high is off or reversed. Uncomment this line to reverse the High/Low setting for the status LED pin.  
    ```//#define CDC_REVERSE_HIGH_LOW```  
    *May be changed through the Web UI or API*
4. Set up the WiFi configuration.  The CheapoDC may operate in either Access Point (AP) mode or Station (ST) mode. The CheapoDC defaults to AP mode when it cannot connect to an access point.  The AP mode SSID will be set to be the same as the hostname which defaults to **cheapodc**.  
**NOTE:** Changing the WiFi configuration is **NOT** recommended. ST Mode settings can be changed in the Web UI while AP Mode settings will be overwritten if Web OTA Update is used.
    * AP Mode settings must be configured in the ***CDCdefines.h*** file:  
      * Change AP mode password. ***DEFAULT: cheapodc***.  
        ```#define CDC_DEFAULT_WIFI_AP_PASSWORD "cheapodc"```  
    * ST Mode settings may be configured in either the ***CDCdefines.h*** file or the ***CDCWiFi.json*** file found in the ***data*** folder. Values in found in the ***CDCWiFi.json*** files will be used before using the values in the ***CDCdefines.h*** file. Using the ***CDCWiFi.json*** file to configure WiFi access allows multiple APs and credentials to be defined. How to configure the ***CDCWiFi.json*** file is found [here](#cdcwifijson) while configuring default values in the ***CDCdefines.h*** file is as follows:
      * Change ST mode SSID. ***DEFAULT: defaultSSID***.  
        ```#define CDC_DEFAULT_WIFI_SSID "defaultSSID"```  
      * Change ST mode password. ***DEFAULT: defaultPassword***.  
        ```#define CDC_DEFAULT_WIFI_PASSWORD "defaultPassword"```
    * WiFi TX Power setting may be optionally modified if you are having issues with an ESP32-C3 board connecting to your WiFi gateway. Set the WiFi TX Power:
      * Enable setting WiFi Tx Power. ***DEFAULT: Disabled***.  
        ```//#define CDC_ENABLE_WIFI_TX_POWER_MOD WIFI_POWER_8_5dBm```  
        Uncomment to enable. If enabled the default value sets TX power to 8.5dbm. Any of the `wifi_power_t` values found [here](https://github.com/espressif/arduino-esp32/blob/master/libraries/WiFi/src/WiFiGeneric.h#L51-L67) may be used. Extensive testing with WiFi TX Power settings has **NOT** been done.

5. The hostname for the CheapoDC may also be changed. Its recommended that this be done using the [Web UI](../README.md#wifi-configuration). This is only needed if you have multiple CheapoDC controllers on the same network. The default hostname in the ***CDCdefines.h*** file may be modified but it will be overridden by any hostname value in the [***CDCWiFi.json***](#cdcwifijson) file.: 
    * Change the default host name. ***DEFAULT: cheapodc***.  
      ```#define CDC_DEFAULT_HOSTNAME "cheapodc"```

>[!NOTE]
>When in access point (AP) mode the SSID for the AP will be the same as the hostname.

6. As of firmware V2.2.0, CheapoDC supports a [Web Update](https://hcomet.github.io/CheapoDC/CheapoDCWebUpdate.html) capability. This is enabled by default but can be disabled by commenting out the following line:  
    ```#define CDC_ENABLE_HTTP_OTA```
7. Do not modify any of the ```#define``` values below the line  ```DO NOT change anything below here```. The Weather Source and OpenWeather API key should be set or changed through the [Web UI](../README.md#web-ui) not in the ***CDCdefines.h*** file.

>[!IMPORTANT]
>**DO NOT** modify the URLs for Weather API or Icon calls.

### Build and Install the Firmware

1. After [configuring the Arduino IDE](#setting-up-your-build-environment), build and upload the firmware to your ESP32.  
   Make sure to have selected the *Minimal SPIFFS (1.9MB APP with OTA/190KB SPIFFS)* partition scheme.  
   **NOTE:** If the *Minimal SPIFFS (1.9MB APP with OTA/190KB SPIFFS)* partition scheme is not listed as one of the partition schemes available for your selected ESP32-C3 board type you will need to select a different board type. Often the AliExpress type boards only list a minimal set of partition schemes. If you do not see the *Minimal SPIFFS (1.9MB APP with OTA/190KB SPIFFS)* in the list of available partition schemes for your board the best recommendation is to select a Dev Module board in the Arduino IDE. For the ESP32-C3 that would be the *ESP32C3 Dev Module*.

2. Optionally, modify the CDCWiFi.json file ([see below](#cdcwifijson)) in the sketch ***CheapoDC/data*** folder to configure WiFi for your network or modify the hostname.

3. Upload the files in the ***CheapoDC/data*** folder using the Sketch data uploading tool. Please READ the following points before uploading the data files.  
   * **LittleFS file system formatting MUST be used for the data upload.**
   * These files are needed for the Web UI as well as configuration of the CheapoDC.
  
### First Time Device Configuration

If you have not modified the default CDCWiFi.json then the CheapoDC will enter AP (Access Point) mode when booted the first time.

* Connect to the access point, SSID: CheapoDC and Password: CheapoDC.
* Browse to the CheapoDC Web UI at [http://cheapodc.local](http://cheapodc.local) to configure your device. When prompted login using the default userid and password: admin, admin. You should be on the [Dashboard](../README.md#cheapodc-dashboard) page.
* Go to the [Device Management](../README.md#cheapodc-device-management) page by clicking on the button at the bottom of the page.
* Scroll down to [WiFi Configuration](../README.md#wifi-configuration) and configure your WiFi SSID and Password. You'll need to [Reboot](../README.md#reboot-device) the CheapoDC for the WiFi changes to take effect.
* After rebooting. The CheapoDC should be connected to your WiFi network. Refresh your browser and stay on the Device Management page.
* Configure the [Controller Outputs](../README.md#controller-output-configuration) if needed. Output 0 and 1 are always dew controller outputs and by default mapped to GPIO pins 0 and 1. Outputs 2 to 5 may be configured as Controller, PWM or Boolean. They are Disabled by default. Outputs **must** be mapped to a GPIO pin first before an [Output Mode](../README.md#output-modes) may be set.  
  For the ESP32-C3 SuperMini GPIO pins 0, 1, 3, 4, 5 and 7 have been validated.
* [Change your password](../README.md#change-password).
* Set up the Humidity Sensor if you have [added one to your device](../README.md#humidity-sensor-configuration). A [Reboot](../README.md#reboot-device) of the device will be required for SDA and SCL pin changes to take effect.  
  For the ESP32-C3 SuperMini GPIO pins 9 (SCL) and 10 (SDA) have been validated.
* [Change the Status LED](../README.md#status-led-configuration) GPIO pin and High Value setting if needed. GPIO pin 8 is the default while setting it to -1 will disable the LED.
* Go to the [Controller Configuration](../README.md#cheapodc-controller-configuration) page to set up the parameters for the dew controller, weather query and your location. Dew controller parameters are explained in the [Dew Control Algorithm](../README.md#how-the-dew-control-algorithm-works) section.

Your CheapoDC should now be ready to use.

## Configuration Files

All the configuration information for the CheapoDC is stored in two files saved to the data partition on the device.

### CDCWiFi.json

This file provides a list of WiFi access points that will be tried by the CheapoDC to establish a network connection. The Hostname and WiFi access point information may be modified using the [Web UI](../README.md#wifi-configuration). This file may also be edited and uploaded using the [File Management](../README.md#cheapodc-file-management) page.

The file content is json formatted using "name":"value" pairs.

`{"hostname":"CheapoDC","connectAttempts":"10","tryAPs":"1","wifi":[{"ssid":"FakeSSID1","password":"Password1"},{"ssid":"FakeSSID2","password":"Password2"}]}`

The example shows settings for two access points in the "wifi" section. This can be 1 or several access points. CheapoDC will step through the list sequentially until a successful WiFi connection is established in Station Mode.

1. Replace "FakeSSID1" and "Password1" for the first AP to try with your first SSID and password.
```{"ssid":"FakeSSID1","password":"Password1"}```
2. To set up a second AP (or more) then update "FakeSSID2" and "Password2" for the second AP (or add more entries separated by commas for more APs). If you only want one AP, then delete the entry including the preceding comma.  
```{"ssid":"FakeSSID2","password":"Password2"}```
3. You can also change the "hostname" from the default of ***cheapodc***.  
```"hostname":"cheapodc"```  
**Note:** Changing the hostname will also change the SSID for the device when in Access Point mode.
4. Changing "connectAttempts" will change then number of times the CheapoDC will attempt to connect to an access point before moving to the next access point in the list.  
```"connectAttempts":"10"```
5. Changing "tryAPs" will change the number of times the CheapoDC will loop through the list of access points before switching to Access Point (AP) mode.  
```"tryAPs":"1"```

If CheapoDC fails to connect to an access point in Station Mode, then it will switch to Access Point (AP) mode. The AP SSID will be the same as the hostname with a default of *cheapodc*. The AP password is always *cheapodc* and can only be changed in the  [***CDCdefines.h***](#configure-firmware-in-the-cdcdefinesh-file) file.

If no ***CDCWiFi.json*** file is found, then the values for WiFi configuration will be taken from the [***CDCdefines.h***](#configure-firmware-in-the-cdcdefinesh-file) file.

### CDCConfig.json

This file is used to save the device and dew controller configuration between power cycles. If the file is not present, then the values defined in the ***CDCdefines.h*** file (the firmware defaults) will be used. The CheapoDC checks for changes to any configuration values every 10 seconds and if a change is detected then the full ***CDCConfig.json*** file will be written to the LittleFS file system on the device.

CheapoDC device and controller configuration may be modified via the [Web UI](../README.md/#web-ui) or the [CheapoDC API](../README.md/#cheapodc-api). The [CheapoDC commands](../README.md/#cheapodc-commands) which support a ***Setter*** function also represent the values stored in the ***CDCConfig.json*** file.

## Web OTA Update Root CA Issue

CheapoDC uses esp32FOTA to detect the availability of a CheapoDC firmware update. The updates are hosted at [https://hcomet.github.io/](https://hcomet.github.io/) on GitHub Pages. The version of esp32FOTA used in CheapoDC V2.2.0 and V2.3.0 required that the root CA for the hosting site be provided to verify the HTTPS link to the site. When the root CA for GitHub Pages was changed after the CheapoDC V2,3,0 release, updates could no longer be verified. Automatic Web OTA Update for V2.2.0 and V2.3.0 stopped working.

CheapoDC V2.3.1 uses the latest  esp32FOTA library which allows for a root CA bundle to be passed and processed to verify the Web OTA Update link. The CA bundle used in V2.3.1 is based on the May 2026 Mozilla trusted CA list. This should prevent future issues with a change in trusted CA at GitHub Pages.

### How to Re-enable Web OTA Update

CheapoDC V2.2.0 and V2.3.0 both support the ability to change the trusted root CA used for Web OTA Update. This is done by uploading a new CA certificate to CheapoDC as a PEM encoded file. If you are currently using V2.2.0 or V2.3.0 follow these steps to perform a firmware update:

1. Get the new root CA by downloading [***root_ca.pem***](https://hcomet.github.io/CheapoDC/root_ca.pem) to your computer.
2. Make sure your CheapoDC is powered up and then browse to the WebUI and logon.
3. Go to the **File Management** page and upload the ***root_ca.pem*** file from step 1.
4. Go to the **Device Management** page and reboot your CheapoDC.
5. Once rebooted, a new firmware release (2.3.1 or newer) should be shown as available under Web OTA Update on the **Device Management** page.
6. Enter your CheapoDC password and click `Update` to complete the update.

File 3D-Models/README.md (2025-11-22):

# 3D Models for CheapoDC

Files that may be used to print cases for the CheapoDC 3-Output and 6-Output builds. Build details may be found in the [build description](https://hcomet.github.io/CheapoDC/CheapoDCBuild.html).

### Notes:

* the holes in the case panels are sized to fit the jacks/switches and LEDs used in the build description. A STEP file is provided so that parts may be modified.
* LEDs are held in the case panels using 3D printed mounts. The mount goes through the front of the panel and then a backer is pressed onto it to hold it in place. The mounts may need adjustment for the size of LED used.

## LED Mount Files

|File|Comments|
|---|---|
|[led-mount-5mm.stl](https://github.com/hcomet/CheapoDC/blob/main/3D-Models/led-mount-5mm.stl)|Mount for LED with 5mm base.|
|[led-mount-6mm.stl](https://github.com/hcomet/CheapoDC/blob/main/3D-Models/led-mount-6mm.stl)|Mount for LED with 6mm base.|
|[led-mount-backer.stl](https://github.com/hcomet/CheapoDC/blob/main/3D-Models/led-mount-backer.stl)|Backer for LED mount.|
|[led-mount-press.stl](https://github.com/hcomet/CheapoDC/blob/main/3D-Models/led-mount-press.stl)|Tool to help press the backer onto the mount.|
|[led-mount.step](https://github.com/hcomet/CheapoDC/blob/main/3D-Models/led-mount.step)|LED mount pieces in STEP format.|

## SHT3x Sensor Probe Files

|File|Comments|
|---|---|
|[sht3x-case-front.stl](https://github.com/hcomet/CheapoDC/blob/main/3D-Models/sht3x-case-front.stl)|Front for SHT3x probe case.|
|[sht3x-case-back.stl](https://github.com/hcomet/CheapoDC/blob/main/3D-Models/sht3x-case-back.stl)|Back for SHT3x probe case.|
|[sht3x-probe-case.step](https://github.com/hcomet/CheapoDC/blob/main/3D-Models/sht3x-probe-case.step)|SHT3x probe case pieces in STEP format.|
|[sht3x-probe-case.3mf](https://github.com/hcomet/CheapoDC/blob/main/3D-Models/sht3x-probe-case.3mf)|SHT3x probe case pieces in STEP format.|

## 3-Output Build Files

|File|Comments|
|---|---|
|[3-output-bottom.stl](https://github.com/hcomet/CheapoDC/blob/main/3D-Models/3-output-bottom.stl)|Bottom for clam shell case.|
|[3-output-top.stl](https://github.com/hcomet/CheapoDC/blob/main/3D-Models/3-output-top.stl)|Top for clam shell case.|
|[3-output-output-panel.stl](https://github.com/hcomet/CheapoDC/blob/main/3D-Models/3-output-output-panel.stl)|Rear Output-panel for clam shell case.|
|[3-output-switch-panel.stl](https://github.com/hcomet/CheapoDC/blob/main/3D-Models/3-output-switch-panel.stl)|Front Switch-panel for clam shell case.|
|[3-output-switch-panel-sht3x.stl](https://github.com/hcomet/CheapoDC/blob/main/3D-Models/3-output-switch-panel-sht3x.stl)|Front Switch-panel with SHT3x sensor jack hole for clam shell case.|
|[3-output-usb-plug.stl](https://github.com/hcomet/CheapoDC/blob/main/3D-Models/3-output-usb-plug.stl)|A press fit plug to cover the ESP32-C3 USB connector hole in the Switch-panel.|
|[3-output-case.3mf](https://github.com/hcomet/CheapoDC/blob/main/3D-Models/3-output-case.3mf)|All case pieces in a single 3mf file.|
|[3-output-case.step](https://github.com/hcomet/CheapoDC/blob/main/3D-Models/3-output-case.step)|3D design file for all case pieces in STEP format.|

## 6-Output Build Files

|File|Comments|
|---|---|
|[6-output-bottom.stl](https://github.com/hcomet/CheapoDC/blob/main/3D-Models/6-output-bottom.stl)|Bottom for clam shell case for the protoboard based ESP32-C3-board.|
|[6-output-bottom-exboard.stl](https://github.com/hcomet/CheapoDC/blob/main/3D-Models/6-output-bottom-exboard.stl)|Bottom for clam shell case modified for the ESP32-C3 SuperMini Expansion Board.|
|[6-output-top.stl](https://github.com/hcomet/CheapoDC/blob/main/3D-Models/6-output-top.stl)|Top for clam shell case.|
|[6-output-output-panel.stl](https://github.com/hcomet/CheapoDC/blob/main/3D-Models/6-output-output-panel.stl)|Rear Output-panel for clam shell case. Includes holes for output LEDs.|
|[6-output-output-panel-noleds.stl](https://github.com/hcomet/CheapoDC/blob/main/3D-Models/6-output-output-panel-noleds.stl)|Rear Output-panel for clam shell case. No output LED holes.|
|[6-output-switch-panel.stl](https://github.com/hcomet/CheapoDC/blob/main/3D-Models/6-output-switch-panel.stl)|Front Switch-panel for clam shell case. Includes holes for output LEDs.|
|[6-output-switch-panel-noleds.stl](https://github.com/hcomet/CheapoDC/blob/main/3D-Models/6-output-switch-panel-noleds.stl)|Front Switch-panel for clam shell case. No output LED holes.|
|[6-output-switch-panel-sht3x.stl](https://github.com/hcomet/CheapoDC/blob/main/3D-Models/6-output-switch-panel-sht3x.stl)|Front Switch-panel with SHT3x sensor jack hole for clam shell case. Includes holes for output LEDs.|
|[6-output-switch-panel-noleds-sht3x.stl](https://github.com/hcomet/CheapoDC/blob/main/3D-Models/6-output-switch-panel-noleds-sht3x.stl)|Front Switch-panel with SHT3x sensor jack hole for clam shell case. No output LED holes.|
|[6-output-case.3mf](https://github.com/hcomet/CheapoDC/blob/main/3D-Models/6-output-case.3mf)|All case pieces and options in a single 3mf file.|
|[6-output-case.step](https://github.com/hcomet/CheapoDC/blob/main/3D-Models/6-output-case.step)|3D design file for all case pieces in STEP format.|

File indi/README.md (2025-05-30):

**INDIlib Driver**

Images referenced by the [indilib.org](https://indilib.org) CheapoDC [driver description](https://indilib.org/aux/cheapodc-dew-controller.html).

Note that up to date documentation for the CheapoDC INDI driver is maintained [here](https://hcomet.github.io/CheapoDC/indi/CheapoDC.html).

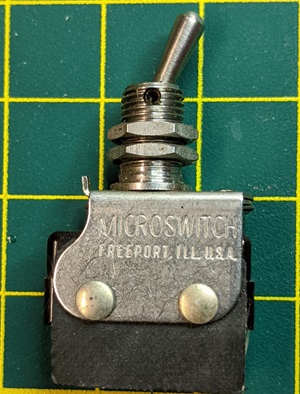
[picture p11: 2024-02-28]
images/toggle.jpg

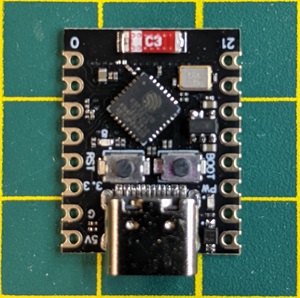
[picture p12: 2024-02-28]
images/esp32-c3.jpg

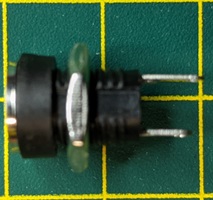
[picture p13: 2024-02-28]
images/5-5x2-1.jpg

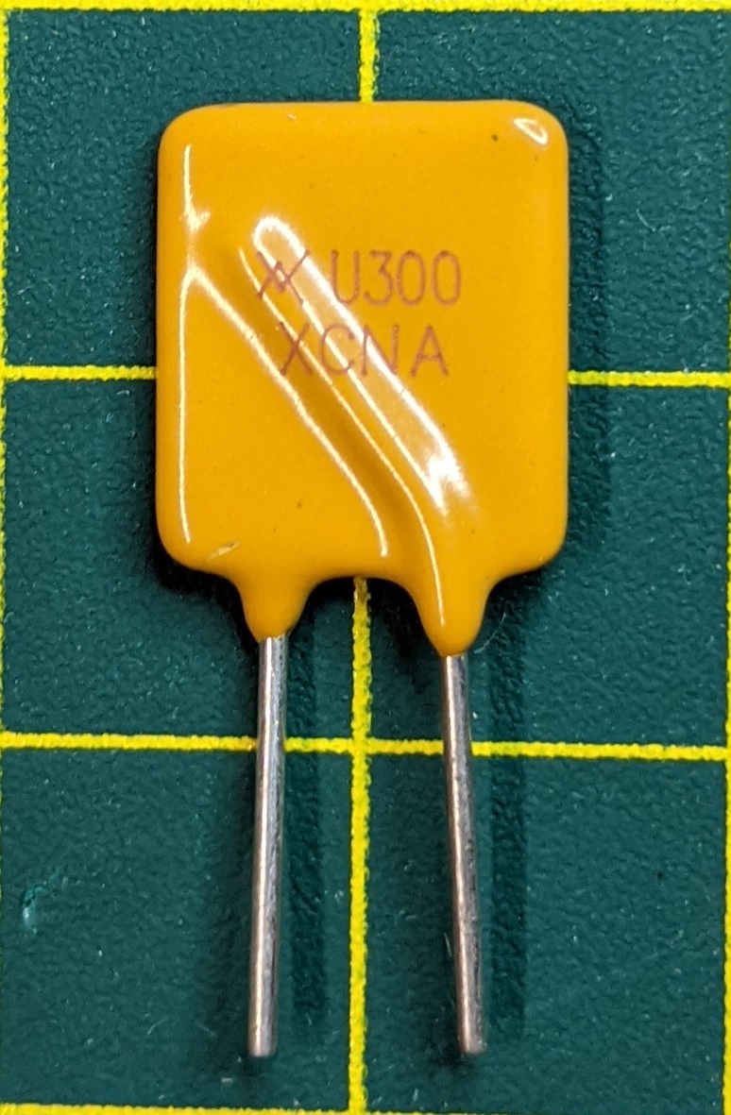
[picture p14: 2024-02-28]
images/pptc.jpg

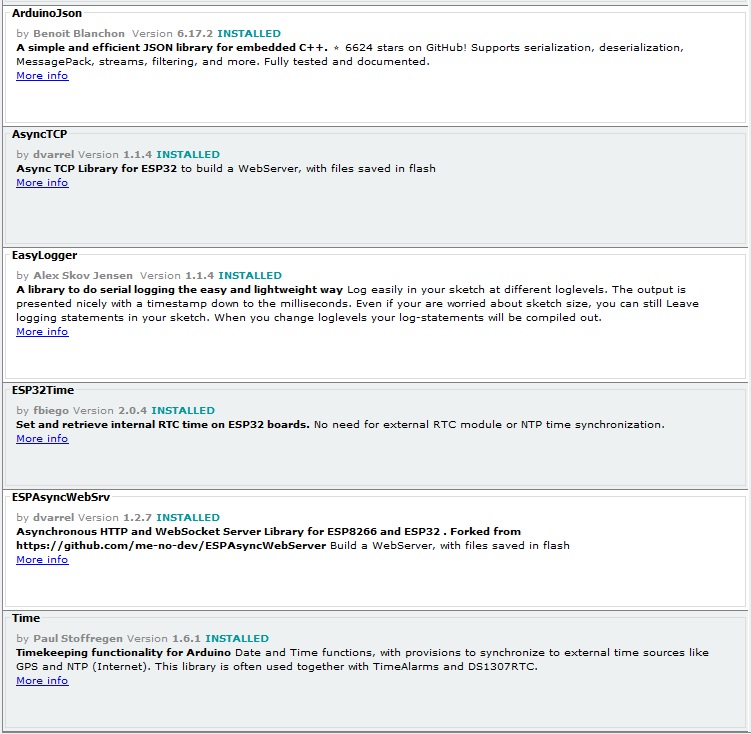
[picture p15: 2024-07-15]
images/CDC-Libraries.jpg

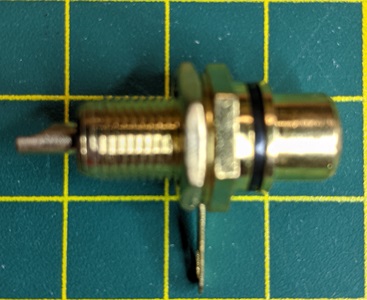
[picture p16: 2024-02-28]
images/rca.jpg

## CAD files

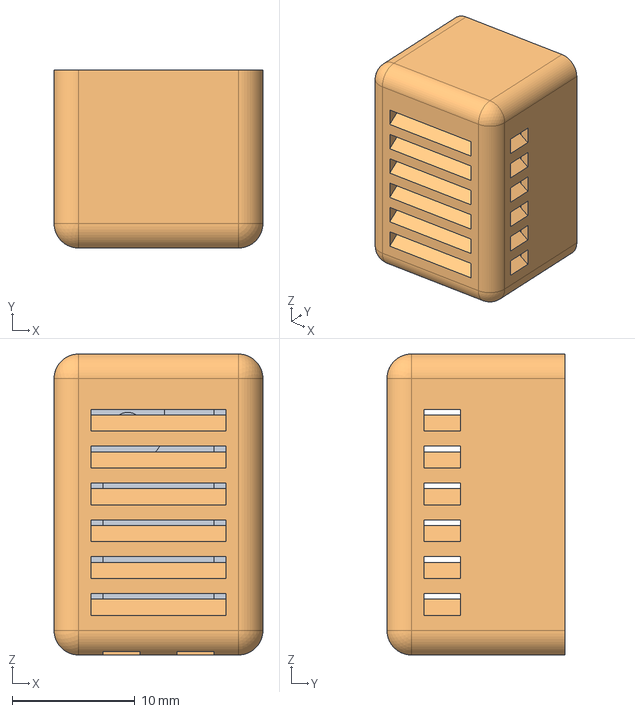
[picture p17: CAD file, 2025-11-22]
3D-Models/sht3x-probe-case.step
17.0 x 14.5 x 24.5 mm

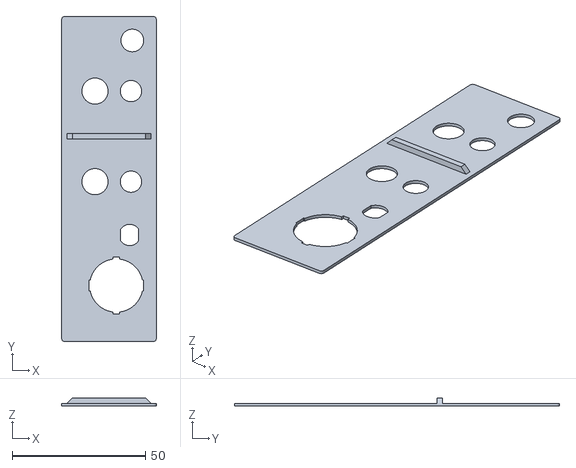
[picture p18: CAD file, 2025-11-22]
3D-Models/6-output-switch-panel-sht3x.stl
35.5 x 122.0 x 3.00

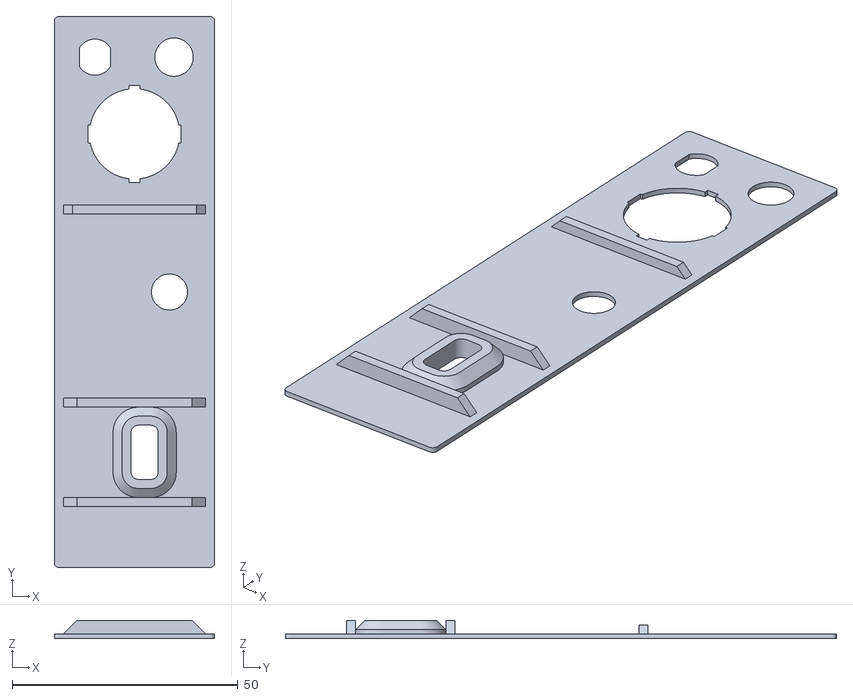
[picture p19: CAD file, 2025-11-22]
3D-Models/3-output-switch-panel-sht3x.stl
35.5 x 122.0 x 4.00

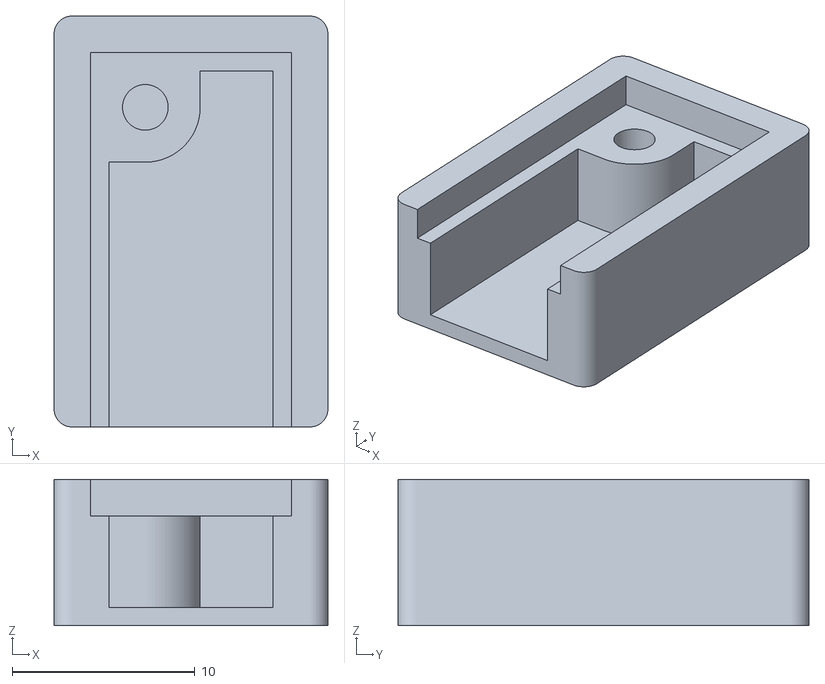
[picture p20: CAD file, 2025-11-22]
3D-Models/sht3x-case-back.stl
15.0 x 22.5 x 8.00

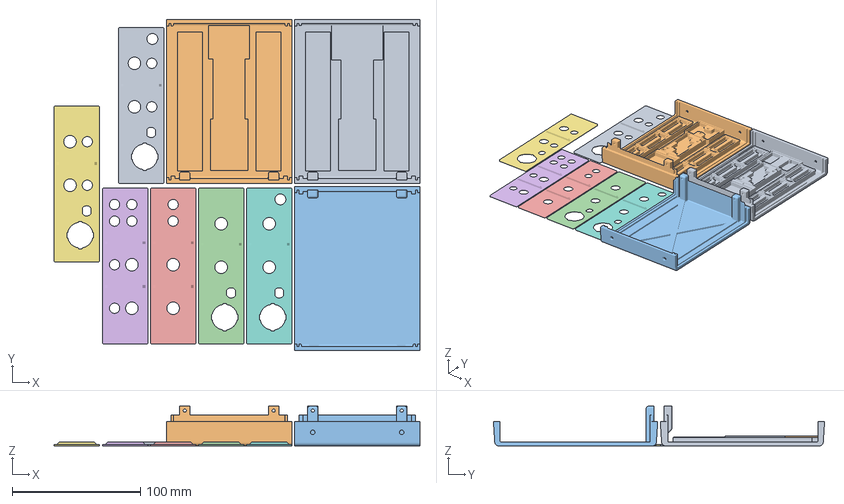
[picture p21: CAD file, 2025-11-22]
3D-Models/6-output-case.3mf
285.8 x 258.6 x 31.0 mm
6-output-bottom-exboard.stl
6-output-bottom.stl
6-output-top.stl
6-output-switch-panel-noleds.stl
6-output-output-panel-noleds.stl
6-output-output-panel.stl
6-output-switch-panel.stl
6-output-switch-panel-noleds-sht3x.stl
6-output-switch-panel-sht3x.stl

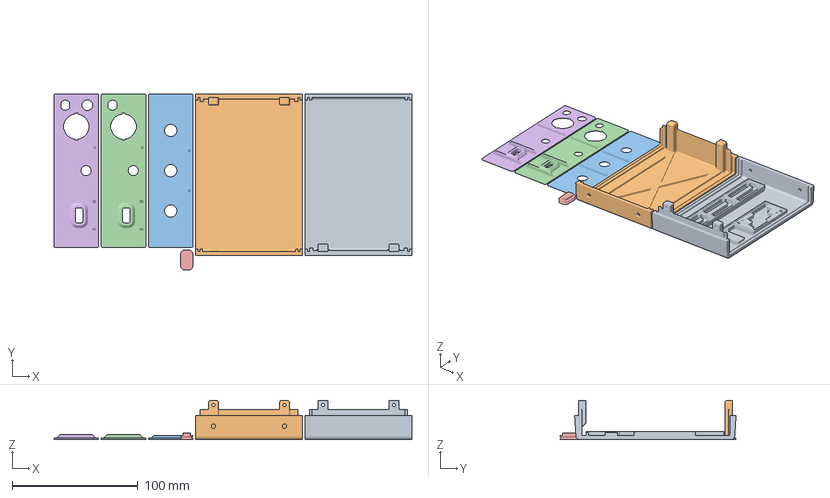
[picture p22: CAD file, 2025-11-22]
3D-Models/3-output-case.3mf
284.5 x 140.0 x 31.0 mm
3-output-bottom.stl
3-output-top.stl
3-output-output-panel.stl
3-output-switch-panel.stl
3-output-usb-plug.stl
3-output-switch-panel-sht3x.stl

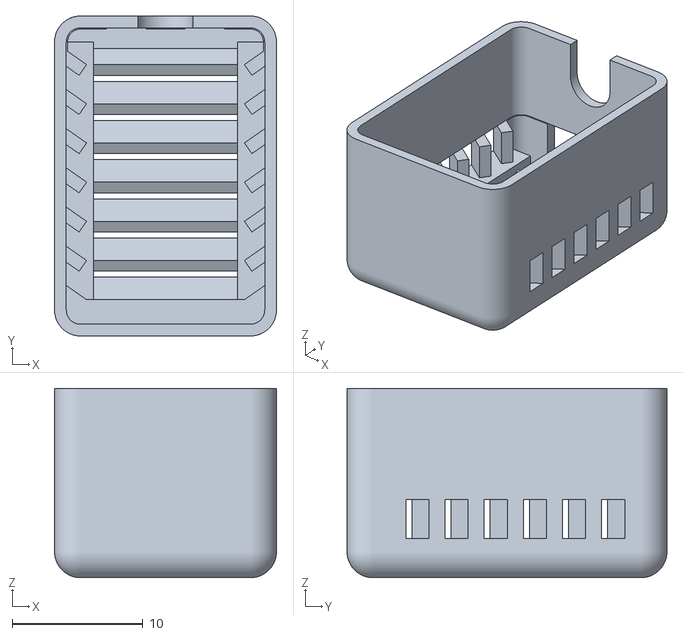
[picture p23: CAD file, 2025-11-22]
3D-Models/sht3x-case-front.stl
17.0 x 24.5 x 14.5

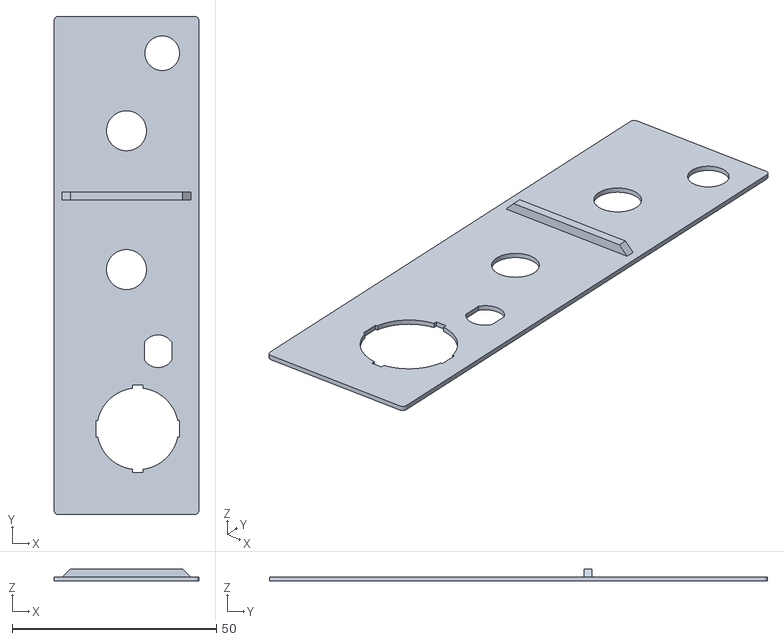
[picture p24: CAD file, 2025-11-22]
3D-Models/6-output-switch-panel-noleds-sht3x.stl
35.5 x 122.0 x 3.00

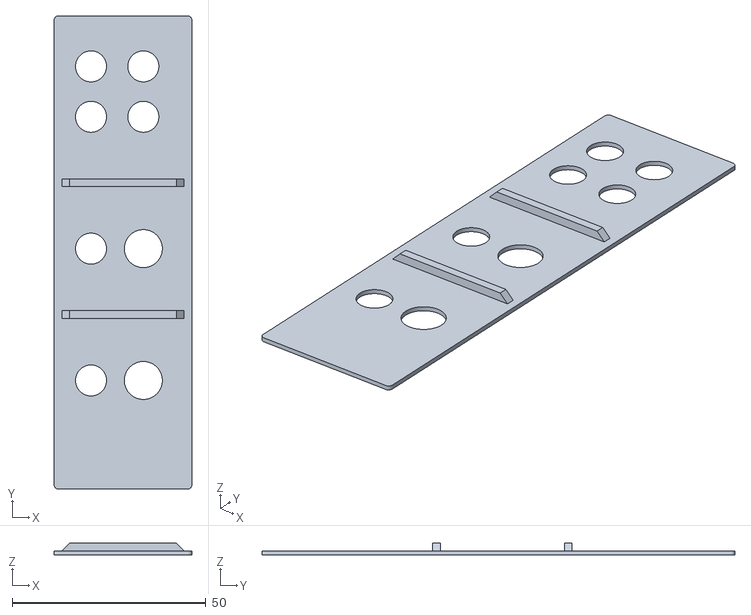
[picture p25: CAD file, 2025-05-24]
3D-Models/6-output-output-panel.stl
35.5 x 122.0 x 3.00

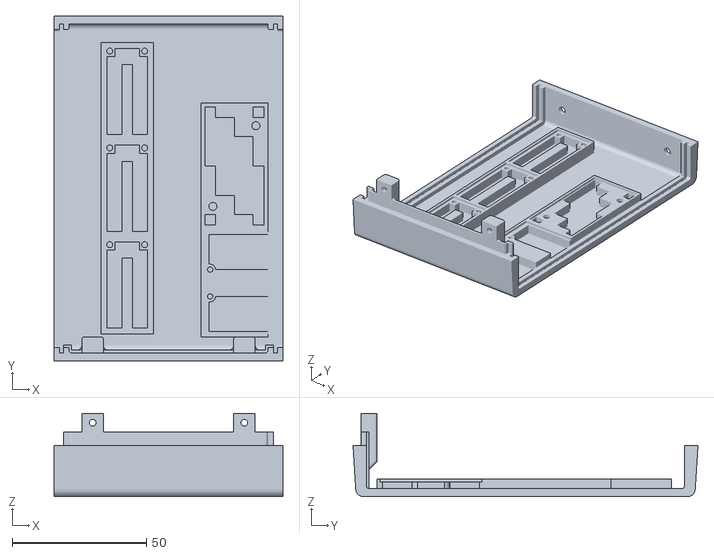
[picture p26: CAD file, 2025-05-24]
3D-Models/3-output-bottom.stl
85.0 x 128.3 x 31.0

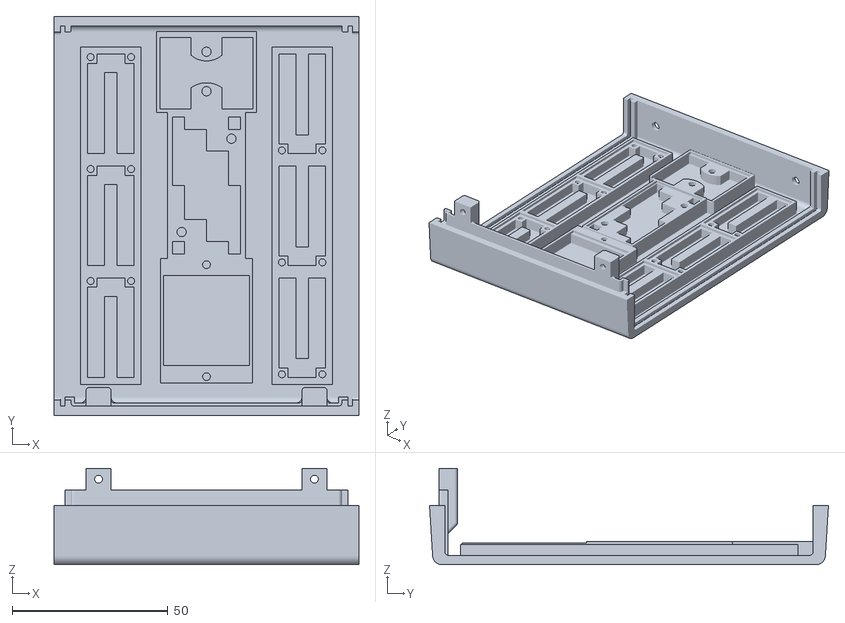
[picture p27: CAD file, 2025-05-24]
3D-Models/6-output-bottom.stl
98.0 x 128.3 x 31.0

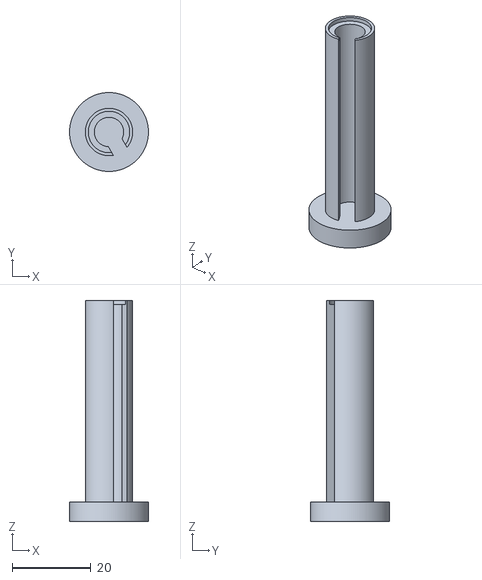
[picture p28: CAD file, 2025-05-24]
3D-Models/led-mount-press.stl
20.0 x 20.0 x 56.0

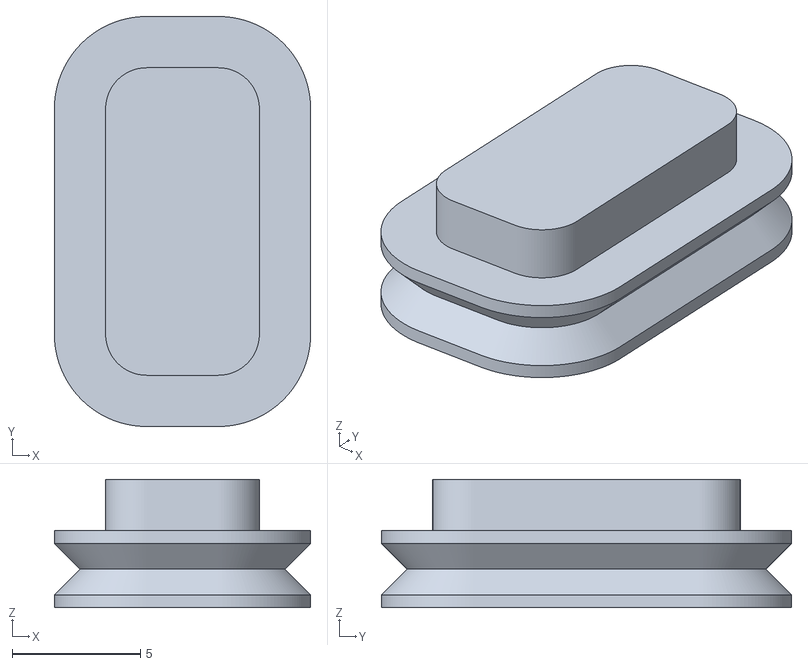
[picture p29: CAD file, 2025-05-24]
3D-Models/3-output-usb-plug.stl
10.0 x 16.0 x 5.00

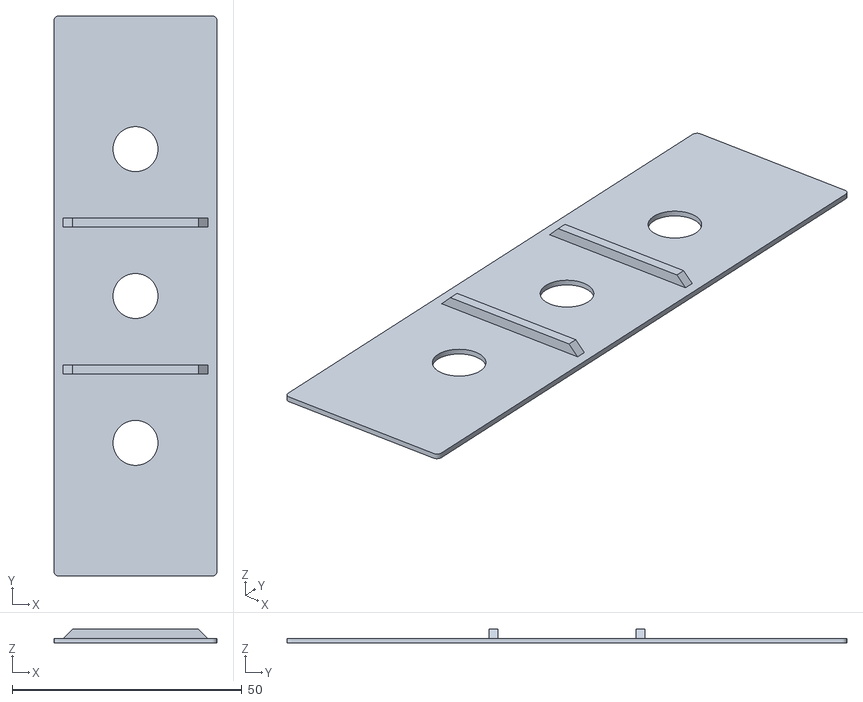
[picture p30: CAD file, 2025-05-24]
3D-Models/3-output-output-panel.stl
35.5 x 122.0 x 3.00

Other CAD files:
3D-Models/6-output-bottom-exboard.stl
3D-Models/6-output-switch-panel-noleds.stl
3D-Models/led-mount-back.stl
3D-Models/6-output-switch-panel.stl
3D-Models/3-output-switch-panel.stl
3D-Models/6-output-output-panel-noleds.stl
3D-Models/led-mount-5mm.stl
3D-Models/led-mount-6mm.stl
3D-Models/led-mount.step
3D-Models/sht3x-probe-case.3mf

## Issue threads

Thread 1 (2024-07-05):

Cannot bring up webpages loaded on ESP32

LordWhiteley-UK, 2024-07-05:
If anyone else has issues, you must use the older (<V2) Arduino IDE eg 1.8.x

Also Make sure that you don't install the latest ESP32 using Board Manager (from Espressif) - Install Version 2.0.17 for example at the latest V3 doesnt support ledcsetup etc

Use this url which describes how to install the ESP32 Data Uploader, by adding esp32fs.jar to \arduino\tools\EESP32FS\tool folder

hcomet, 2024-07-06:
Yes, I think the Espressif 3.0.x versions started rolling out in may. The build README.md does indicate "use the Espressif version 2.0.x".

I'll admit that I mainly did my development using VSCode with the Arduino plugin. I my check Arduino IDE version was 1.8.19. Should have noted that in the build information

I also note that I did not list ArduinoJSON as a required library. Version 6.x of ArduinoJSON must be used. Version 7.x came out after I published this project. Version 7 has a different memory management model and deprecates dynamicJSON documents which I use.

I just did a fresh install of the 1.8.19 IDE on a new machine and installed a clean set of libraries with appropriate versions. Seems to compile with only the C++17 structured binding warning which is not an issue for the ESP32 compiler.

I'll need to update the build information.

Any other issues?

LordWhiteley-UK, 2024-07-06:
Thankyou for your reply :) yes I realised I needed Arduinojson.h too :)

It’s a blinkin pain that libraries get up-issued but don’t maintain backward compatibility. It took me a while to realise the ledcsetup error was caused because I was using the latest esp32 v3.x in board manager but needed to install v2.x or earlier version :)

Anyway, I managed to compile and upload the firmware and then upload the web interface by uploading the data folder. I’m using the esp32-c3 developer for the board selection with all the board settings left at default

I can see cheapodc on my router and tried connecting using cheapodc.local. So far so good.
I then get the a login dialogue and enter admin, admin.

However, after this nothing?? In fact re-trying cheapodc.local just throws up an error “can’t find webpage” or something similar.

Checked on router and cheapodc is still showing. So it appears after trying to login, no other webpages from the esp32 can be accessed. I haven’t enabled the web socket API, I don’t really know what’s that’s for.

I don’t if this is because I need to change anything in the Arduino esp32-c3 developer board setup menu?? As I said everything is at default including the esp32 internal memory partition.

It a really neat project which is why I’d really like to get it working - it’s really close to working :)

 PS I’ve designed a 3D printed box on Fusion360 and I’ll stick on Prusa projects  or Thingiverse at some point. 3D printers for Astrophotographers are so useful:)

hcomet, 2024-07-06:
You can try a couple of things:

1 - Monitor it through the serial monitor in the IDE. If you don't see anything then you can increase the level of debug messages by changing the logging level in CDCDefines.h. Change "#define LOG_LEVEL LOG_LEVEL_ERROR" to "#define LOG_LEVEL LOG_LEVEL_INFO" to start.

2 - You can change the weather API service to OpenMeteo so that no API key is needed. Comment out "#define CDC_USE_OPEN_WEATHER" in CDCdefines.h.

3 - confirm that the Blink LED default of 8 will actually work for you. The ESP32-C3 boards seem to be all over the place for pin usage. If pin 8 is used for something else then it may be causing an issue. You try using the blink sketch to see what the right pin is.

hcomet, 2024-07-06:
Okay, I don't have a spare C3 to play with but I did an OTA upload of the image I built using the clean install with clean libraries to one of my completed dew controllers. It seemed to work fine using either Weather API service. I was using a a preconfigured CDCWiFi.json with my network setup.

Not sure why, but I couldn't find the exact libraries that I seemed to have in my original build environment. It may be a difference between the VSCode arduino library manager and the IDE library manager. Here's the libraries I installed with the Arduino IDE library manager:
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

LordWhiteley-UK, 2024-07-06:
Many thanks i will compare with my installed libraries :)
Swapping to OpenMeteo didn't make any difference - I havn't tested using an off board LED (yet)
Oddly, I get absolutely nothing from the serial monitor ???? Just stays blank which is very odd - I did made the changes to the CDCDefines.h as you suggested, but still no serial monitoring.
It's just strange that I can power up the ESP32 and is clearly connecting to my home network using station mode. And I can get a login dialogue to come up. It just doesn't go the config webpage, after entering admin & admin.
I have definately uploaded the "data" folder, which contains the web pages eg config etc I dont know whether you can remotely check that the data folder exists and that all the webfiles are there.

FYI - The ESP32C3 I bought is this one from Amazon one (https://www.amazon.co.uk/gp/product/B0D2DH1F1H/ref=ppx_yo_dt_b_search_asin_title?ie=UTF8&psc=1)

Although experience of trying to get an Onstep system working with a ESP32 R32 - some boards just wont work

hcomet, 2024-07-06:
A lot of people have had issues with the serial monitoring. If you haven't try to enable USB CDC on Boot.

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

Also, you could try another ESP32 if you have it. I have compiled and run on both the S3 and classic versions. I only used the C3 for the size and price.

hcomet, 2024-07-08:
Ok, pulled the C3 from one of my dew controllers. I played around and I'm wondering if the issues is the file system.

I unfortunately did NOT point out in the build instructions to use the data uploader but I also did not mention that I used LittleFS as the file system. NOT SPIFFS. If you installed the older data uploader tool then it only supports SPIFFS. You need the tool found
[here](https://github.com/lorol/arduino-esp32fs-plugin/releases) - (https://github.com/lorol/arduino-esp32fs-plugin/releases).

This assumes that you modified the CDCdefines.h to set up your WiFi credentials, since uploading using SPIFFS the CDCWiFi.json would not be readable and the CheapoDC would not connect to your router.

If I follow the above path:
- change the CDCdefines.h WiFi info to my AP
- build and upload
- then upload data as SPIFFS

The CheapoDC will connect to my AP, I will be able to log into it BUT it cannot read the filesystem and cannot load the web pages.

As a side note, you need to flip to the serial monitor as soon as the reset via RTS message comes up completing the data upload. Then you should catch the LittleFS filesystem error. If you wait at all then not much gets logged so may look like the serial monitor is not working (Also serial baud rate is 115200 which may be different than your upload baud rate.

In any case hopefully this is the problem you are seeing. Use the tool that supports LittleFS. Upload the data as LittleFS and it should all work. I've been switching back and forth to try things out and switching to LittleFS always fixes things.

LordWhiteley-UK, 2024-07-08:
Many thanks for the continued support :)

I did actually add the eps32fsjar file to tools/ESP32FS/tool folder but I only have one option in the Arduino tools menu  ie ESP32 sketch data upload. When I click on this is seems to upload and then says SPIFFS image uploaded. I don't get the option of using LittleFS '??

I dont get a drop down menu giving option of SPIFFS, LittleFS or FATfs???

I have tried your link and swapped the esp32fs.jar files but it still only uploads SPIFFS & this is the only option on the memory partion ?

- so I think this is the issue here?. BTW I do have some additional ESP32 modules on the way just in case this generic one is a bummer

hcomet, 2024-07-08:
Yes, if it is only allowing for SPIFFS then that will be your issue. I'm not sure that using another ESP32 module will change whether or not the file system selector shows up. You could try deleting the esp32fs.jar then restart the Arduino IDE. That should remove the tool from the IDE Tools drop down. If it doesn't then the IDE is picking it up from somewhere else.

I did see that there is a LittleFS data upload tool available for Arduino 2.2.1 or higher. But I have not used the 2.x IDE or this uploader.
https://randomnerdtutorials.com/arduino-ide-2-install-esp32-littlefs/

LordWhiteley-UK, 2024-07-08:
I rolled back from Arduino IDE v2 but maybe I need to re-try this.
There are other files mentioned that I haven’t installed ie mklittlefs.exe
I’ve been using Ralf S Bacons instructions - https://github.com/RalphBacon/203-SPIFFS-vs-LITTLEFS

LordWhiteley-UK, 2024-07-08:
At last it's working !! I now manged to get the drop-down menu to be able to select littleFS

I removed Arduino IDE and re-installed
(I retained the libraries under by sketch directory as indicated in Preferences. ie in my case C:\Users\jps\OneDrive\Documents\Arduino\libraries\
In there are the following folders
AduinoJson, AsyncTCP, EasyLogger, ESP32Time, ESPAsyncTCP, ESPAsyncWebSrv & Time

Under C:\Users\jps\OneDrive\Documents\Arduino\tools\ESP32FS\tool is esp32fs.jar
(downloaded from https://github.com/lorol/arduino-esp32fs-plugin/releases)

ESP32 board link that is pasted in Addition Board URL's in Preferences is https://espressif.github.io/arduino-esp32/package_esp32_index.json

hcomet, 2024-07-08:
That's great to hear.

I also tried out the Arduino IDE V2.3.2 with the LittleFS uploader mentioned in the link above. Using the latest 2.0.x Espressif version with libraries above seemed to work fine. A couple had newer subversions which also seem fine as long as you stay within the major version.

I'll work on updating the build documentation and then close this off.

Good luck and thanks for trying out the CheapoDC.

hcomet, 2024-07-15:
Fixed in release v1.0.2

LordWhiteley-UK, 2024-07-15:
Very Nice Work !!! Thankyou very much for your efforts !!

hcomet, 2024-07-16:
Yes, you are correct the diagram doesn't seem to match the wiring in the completed implementation image.

I'll have to update the diagram.

Thanks again.

hcomet, 2024-07-16:
Ok, diagram updated. Not going to create a new release since there are no code changes and its on the main page for the project in GitHub.

Thanks again.

Closed 2024-07-15.

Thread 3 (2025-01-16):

Error opening nonexistent file CDCConfig.json

makahlow, 2025-01-16:
I'm not able to compile a working firmware.

When the program starts, I get

000:00:00:02:018  ALERT     [setup] : Initializing CheapoDC.
000:00:00:02:591  ALERT     [_connectWiFi] : cheapodc.local connected to: Oak with IP address: 192.168.1.92
000:00:00:02:592  ALERT     [_connectWiFi] : mDNS responder started
000:00:00:02:596  ERROR     [LoadConfig] : Failed to open: /CDCConfig.json
000:00:00:02:596  ERROR     [Main-setup] : Load Configuration Failure. Will continue on defaults.

assert failed: tcp_alloc /IDF/components/lwip/lwip/src/core/tcp.c:1851 (Required to lock TCPIP core functionality!)

There is no CDCConfig.json file in the data folder.

I am able to get littlefs to work in the example files, along with several wifi and networking examples.

I have had to use a memory model with no OTA in order to get it all to fit in memory. The script references a partitions.csv file, but it is not included in the download.

FYI I am using this board - https://www.amazon.com/dp/B0CW62PPZ1?ref=ppx_yo2ov_dt_b_fed_asin_title&th=1. I have attempted to load the software on two separate boards without luck.

hcomet, 2025-01-16:
The CDCConfig.json file is no longer included in the download and is not needed for the first run of the firmware. If the CDCConfig.json is not present then the defaults set in the CDCdefines.h file will be used. These are built into the firmware. As soon as configuration changes are made (via the web interface or API) the CDCConfig.json will be saved to the LittleFS file system.

Your issue seems to be related to the assertion error:
`assert failed: tcp_alloc /IDF/components/lwip/lwip/src/core/tcp.c:1851 (Required to lock TCPIP core functionality!)`

You didn't mention in your issue which ESP32 Arduino Core version you are using but the assertion error seems to be related to the latest versions of this library, 3.1.0 and 3.1.1 (released in the last month). There are reports of ESPAsyncWebServer failing with the latest ESP32 core. See, [1455](https://github.com/me-no-dev/ESPAsyncWebServer/issues/1455).

CheapoDC makes use of the ESPAsyncWebServer library and there doesn't seem to be a fix available yet. The work around seems to be to back down the version of ESP32 core. Assuming that you have installed either 3.1.0 or 3.1.1 ESP32 core in your Arduino IDE then go back to version 3.0.7 and try rebuilding the CheapoDC. This can be done in the Arduino IDE Boards Manager.

There have also been some reports of 3.1.x increasing build sizes so that may also be your issue with the size of the build. I haven't seen anything related to partitions.csv though. The partitions.csv file is not downloaded though. It is created as part of the build environment based on the ESP32 board you selected in the Arduino IDE and the Partition Scheme.

Try rebuilding with "esp32 by Espressif Systems" version 3.0.7.

hcomet, 2025-01-26:
Note: Arduino core for ESP32 3.1.x now supported with [CheapoDC v2.1.0](https://github.com/hcomet/CheapoDC/releases/tag/v2.1.0)

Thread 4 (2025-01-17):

No PWM signal output on pins 0 or 1

makahlow, 2025-01-17:
Thanks again for the help on the issue of compiling

Sorry for the bother, but I've got another issue... The program compiles, connects to my wifi, the web interface works, accesses the weather site, all that. Everything appears to work, except that I'm not getting anything from GPIO0 or 01. Nothing. I've tried subbing other pins (20 & 21) but they don't work either; I've also tried it with a different ESP32-C3 module that's not been used in a circuit. Same result.

I've built the circuit. I can manually turn on the MOSFETs by applying 3.3V on the trigger/pwm input, and then I get the 12V output as expected.

Everything looks great, it's just that *one little thing* (which I'm hoping is very simple).

hcomet, 2025-01-17:
Maybe a dumb question (comment) but make sure that this line is NOT commented out in CDCdefines.h:
`#define CDC_ENABLE_PWM_OUTPUT // comment out to disable output pins (mainly for debugging)`

If it is commented out then everything will look like its working but no PWM signal is ever sent.

Also, if you haven't tried it yet, switch the Controller Mode to Manual using the Web UI. Then set the Output to something greater than zero. This should force a PWM signal if its working.

Finally, you can try turning on the debug logging, This can be done in the CDCdefines.h.  Change:
`#define LOG_LEVEL LOG_LEVEL_ERROR`
to
`#define LOG_LEVEL LOG_LEVEL_DEBUG`

This will generate A LOT of console logging so you could also filter it down to the functions that set the PWM output by uncommenting and changing:
`// #define LOG_FILTER "handleWebsocketMessage,processor,getCmdProcessor,SaveConfig,processClientRequest"`
to
` #define LOG_FILTER "dewController,updateOutput"`

That should show which pins are set for PWM and when PWM values are changed in the the console log.

Then manually change the output using the Web UI to see of the changes are echoed in the logging.

hcomet, 2025-01-17:
Alright, I found the issue. I had a copy/paste error that I fixed and I obviously messed up the check in. I'll get the fix up tonight.

makahlow, 2025-01-18:
Thanks!

hcomet, 2025-01-18:
Committed a fix. Grab the new [CDController.cpp](https://github.com/hcomet/CheapoDC/blob/main/CheapoDC/CDController.cpp) and give it a try.

If it all works I'll put out a 2.0.1 release with the fix.

makahlow, 2025-01-18:
Thanks! That appears to work! I'm getting a voltage on the pins which varies with the power applied. Any problems I have taking this to 12V w the MOSFETs is my own problem. ;-)

hcomet, 2025-01-18:
Great to hear. I'll create a release. I did a full retest myself. I use an LED wired for 12V on the MOSFET outputs to make sure it all works since the dew heaters have a bit of lag.

hcomet, 2025-01-18:
Fixed in release [v2.0.1](https://github.com/hcomet/CheapoDC/releases/tag/v2.0.1)

Closed 2025-01-18.

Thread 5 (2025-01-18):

No PWM on GPIO01...

makahlow, 2025-01-18:
My apologies for not checking this out further before saying it was "done".

I only tested the output on pin 1 (GPIO 0). That works with the new patch 2.0.1. Pin 2 (GPIO 1) does not. When I swap the pin definition in CDCdefines.h to

#define CDC_PWM_OUTPUT_PIN1 1  // set first Output Pin
#define CDC_PWM_OUTPUT_PIN2 0  // set second Output Pin or comment out to disable

(swapping 1 & 2), then it's GPIO 0 that does not work.

hcomet, 2025-01-18:
Another dumb error but I definitely tested both outputs on my device and they both worked. The code definitely shouldn't have worked. It was related to adding support for the latest ESP Arduino Core and my test device is one i upgraded from a previous working release on Core 2.x. I wonder if Pin attachments to PWM channels stay through reboots and power cycles. That would be the only explanation for mine working.

In any case the fix was simple but of course confirming it works would require a fresh chip. Again give the latest version of [CDController.cpp](https://github.com/hcomet/CheapoDC/blob/main/CheapoDC/CDController.cpp) a try.

hcomet, 2025-01-18:
Spent the morning trying to get my device to fail on the second channel. Erased the flash on the C3, tried to detach the channels in code, checked for a short between the pins. The previous code was not setting the second pin properly but it seems that once a pin is attached to a channel it stays there until attached somewhere else. Fix I committed last night should fix it. Added some extra error checking this morning. That's in the latest commit.

Sorry for the issues.

makahlow, 2025-01-18:
Thanks, and no apologies needed. It works now.

On another note - I was having real trouble connecting to wifi, oddly
enough only when the ESP32 was installed in the breadboard. I found a
solution & added the line WiFi.setTxPower(WIFI_POWER_8_5dBm); to the
CDCSetup::_connectWiFi routine, and it cures the problem.

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

hcomet, 2025-01-19:
Glad to hear its working.

I have not had any issues with WiFi connectivity but Google indicates that there are versions of the C3 mini boards that have this issue. Happy to add this as a compile time flag in the CDCdefines.h. Something like:
`//#define CDC_ENABLE_WIFI_TX_POWER_MOD WIFI_POWER_8_5dBm // Uncomment to adjust WiFi TX power if you are having connection issues`

Did you add it around line 499 after the connection is established?

Also, related to the first issue you had with the v3.1.x version of Arduino Core. I did some more digging and I may have to move to a different implementation ESPAsyncWebServer that seems to be keeping up with the Espressif changes better. I'll have a look at that later this week.

hcomet, 2025-01-19:
Okay, added/committed the WiFi TX power setting as an option in the CDCdefines.h and put the call right in after the WiFi.begin(...);

Will put out a v2.0.2 release later to close this off.

Thanks.

hcomet, 2025-01-20:
Fixed in v2.0.2 release.

Closed 2025-01-20.

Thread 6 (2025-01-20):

Support ESP32 for Arduino Core v3.1.x

hcomet, 2025-01-20:
ESP32 for Arduino Core v3.1.0 released in Dec. 2024 and then v3.1.1 in Jan 2025 impacts CheapoDC in the following ways:
1. Version of ESPAsyncWebServer used is impacted by changes in core v3.1.x causing
    `assert failed: tcp_alloc /IDF/components/lwip/lwip/src/core/tcp.c:1851 (Required to lock TCPIP core functionality!)`
    * will need to move to the [ESP32 Asynchronous Networking](https://github.com/ESP32Async) version which looks to be active and more tightly tracking ESP32 for Arduino Core development. The 3.6.0 version of ESPAsyncWebServer works with core 3.1.1 but requires code and library setup changes to use.
2. Increases the size of the firmware executable to 98% of the default partition scheme
    * simple upgrade should be fine but enabling Debug logging or WebSocket support makes the executable too large.
    * Will need to move to a minimal SPIFS partition scheme which will break OTA upgrades and is not listed for all ESP32-C3 board variants.

hcomet, 2025-01-23:
Point 1. now complete for default CheapoDC configuration. Move  to core v3.1.x and ESPAsync version of ESPAsyncWebServer complete with this [commit](https://github.com/hcomet/CheapoDC/commit/564d31f8c35c7bf3ac13aa70bc23045b10df8903).

Unfortunately this has put the executable firmware size at the limit for the default 4MB partition scheme for ESP32C3. Neither Debog logging nor WebSocket support may be enabled.

Will need to move to minimal SPIFFS partition or a custom partition to increase ota_0/ota_1 sizes.

Closed 2025-01-26.

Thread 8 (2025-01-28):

No web access?

LordWhiteley-UK, 2025-01-28:
So,
(1) Downloaded CDCConfig.json and CDCWiFi.json files from original V1 Cheapodc
(2) CDCConfig.json and CDCWiFi.json files pasted into data folder
(3) Sketch successfully compiled on latest Arduiino IDE and uploaded to my ESP32-C3 without any error.

However, although Cheapodc appears on my network, I cannot open a webpage ie http://cheapodc.

Looking at the Serial Monitor port on the Arduino IDE application, it appears that the ESP32-C3 starts up and generates a whole lot of code BUT then reboots and repeats generating the same code before rebooting again….

hcomet, 2025-01-28:
Okay, a lot of changes between v1.0.3 and the latest v2.1.0. To re-conform it works, I just did a fresh install of v1.0.3 on an ESP32C3 board, configured it and then went through the upgrade steps to take it to v2.1.0. It did work. The first time it booted after the upload of v2.1.0 it did crash and reboot on a LittleFS mount issue. Likely this was caused by the change in partitioning required for v2.1.0. When the LittleFS mount fails then a format of the partition is forced and then a reboot. After this happened I had no issues with the upgraded CheapoDC.

Can you confirm the following:
* make sure you have switched to the new versions of the libraries as outlined in the [Setting Up Your Build Environment](https://github.com/hcomet/CheapoDC/blob/main/CheapoDC/README.md#setting-up-your-build-environment). The old versions don't all work with the latest Arduino core for ESP32.
* In particular make sure you have switched to the new ESPAsyncWebServer and AsyncTCP from Me-No-Dev. The versions from dvarrel do not work with Arduino core for ESP32 version 3.1.x.
* Also, make sure you have the dvarrel versions of the library uninstalled. If the compiler selects the wrong AsyncTCP then it will build but it will crash at runtime.
* Make sure you have the Arduino IDE set properly for the upgrade:
   1. The first time you build and upload make sure that you erase all the flash with: *Erase All Flash Before Sketch Upload: "Enabled"*
   2. Also make sure you've selected the new partition scheme: *Minimal SPIFFS (1.9MB APP with OTA/190KB SPIFFS)*

When the CheapoDC boots the first couple of lines in the Serial Monitor should be similar to:
```
000:00:00:02:017  ALERT     [setup] : Initializing CheapoDC.
000:00:00:02:021  ALERT     [CDCSETUP] : LittleFS Mounted. Size: 131072 Used: 114688
```
Showing that the LittleFS partition mounted and the size. The new partition scheme leaves a very small partition and the data folder with configuration files just fits with about 16K to spare.  Since you said you were getting a lot of output, I assume you're getting past this point so it may be a library version mismatch.

If you're still having problems, upload a copy of the Serial Monitor log with the rebooting.

LordWhiteley-UK, 2025-01-28:
Many Thanks for your reply Stephen :)

It's now working :)
All I had to do was to **_remove_** AsyncTCP by dvarrel from the Arduino IDE
And that fixed it !!
Many Thanks - I must get around to designing a PCB to carry all the electronics :)
Cheers
John

hcomet, 2025-01-28:
No problem John. You're not the first person to have the wrong AsyncTCP in the build path. I'll add an additional note in the upload section asking people to look at the build environment notes.

Glad to hear its working and thanks for using the CheapoDC.

BTW: I have a favour to ask. If you have the time, could you update your review comments for the CheapoDC on the Stellarmate site. The comments currently make it look like you never got it to work.

Thanks,
Stephen.

LordWhiteley-UK, 2025-01-28:
I have asked (emailed) Stellarmate to delete my review, as I cannot change it or add a new review ???

hcomet, 2025-01-28:
Thanks for looking. I had also looked to see if I could add a comment but couldn't.

hcomet, 2025-01-28:
Comment added to upgrade section in readme to check library versions and to check for multiple installed versions of AsyncTCP.

Closed 2025-01-28.

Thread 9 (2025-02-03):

Request in a future iteration

LordWhiteley-UK, 2025-02-03:
Not an issue but a suggestion.
It would be cool to have say 4 MOSFET switches controlled by the ESP32-C3.

You could add say a 0.1ohm in series with each MOSFET and add to the GUI whether switch was on or off and if on, the current draw.

You could add devices eg Camera, mini PC etc and have control over them.

I’m not a coder but the additional circuitry would need 12V divided down for GPIO and each output of the 0.1ohm resistor would also need dividing down.

Or just have a function to turn on or off the 4 output MOSFETs

The PCB I’m designing for the Cheapodc, has 4 DC output that have a 3Amp resettable fuse in series with each, but of course these will always be on.

Anyway it’s just a thought :))

Ps still trying to get stellarmste review removed..

hcomet, 2025-02-03:
I've had similar thoughts about expanding the capabilities of the CheapoDC but more in line with staying with the dew controller focus of the device. Things like adding additional PWM ports or temperature sensor ports etc... Ultimately the issue comes down to what the goal of the project was, a "cheap and easy" dew controller. A basic dew controller that can work for your main telescope and your guide scope which is fairly easy to assemble from low cost "off-the-shelf" parts.

Although good ideas, adding controlled power ports would also be stepping out of the original goal or focus of the project. I think they would also move it more into the area of a power box versus a dew controller. There are projects out there doing power boxes. There was one being built with a lot of discussion on the indilib.org forum about a year ago. I took a quick look but couldn't find a link though.

I can also recommend the projects by Robert Brown. I've built both his myFPESP32 focuser and myDCP4ESP32 dew controller. I wrote the INDI driver for the dew controller. His projects are on [Sourceforge](https://sourceforge.net/u/brownrb/profile/) and his [ESP32DB](https://sourceforge.net/projects/myesp-boards/) project looks like it may be more in line with what you are looking for.

Having said all of that... There may be room for a CheapoPB (Cheapo Power Board) type project separate from this one. I do have a couple of things I'd still like to do for the CheapoDC though. In particular move things like PIN assignment to runtime control from compile time options. I'd like to be able to provide executable firmware installable from the web using ESP32 Web Tools so more runtime flexibility is needed.

Thanks for the ideas. Also, don't worry about the Stellarmate review. You put in your request and now its out of your hands.

LordWhiteley-UK, 2025-02-03:
Yes, I guess I was looking at more of a "Power Box" but your Cheapodc is a unique way of doing a dew controller.

Yes you could add a thermistor & humidity sensor and not rely on real time internet data but that would be the conventional way of doing it.

It's just with your design, you could simply wire 4 more MOSFET boards to the ESP32, and be able to switch things on/off :) (Current monitoring is not really necessary). The hardest part would be the programming - I cant remember how the Pegasus power box was set up, but I'm sure I used to use one to switch everything off at the end of a NINA imaging session.

I've pretty much designed a PCB for the Cheapodc, I just need to double check the dimensions of the Sourcing Map BNC connectors (As I had to generate the PCB layout by measuring).

I'm also torn with using a linear regulator (LM7805) or a MP1584EN based regulator ? I might go with the MP1584EN as it doesn't need many parts. When I've ordered the PCB's I can rattle off another 3D printed box for it :)

Anyway, the latest version of the Cheapodc was way more easier to setup than the earlier version :)

Many Thanks for all your hard work :)

hcomet, 2025-02-03:
Yes, adding additional control pins is somewhat easy on the hardware side but would require adding control to the web pages, API and probably the INDI driver so they would be usable. Robert Browns ESP32DB is set up this way with runtime configurable pins that can be set to be simple on/off or PWM and whether default state is on or off.

You may want to add a couple of MP1584En based regulators. One to drive the ESP32 and maybe some ports at 5V and one that is adjustable for a variable output. ie: if using a DSLR for a camera they are often voltages  like 7V to 9V.

hcomet, 2025-02-13:
FYI: The commit to the CheapDC-Plus branch seems to be mostly working. You can try it if you'd like by grabbing the [lastest](https://github.com/hcomet/CheapoDC/archive/refs/heads/CheapoDC-Plus.zip) from that branch.

Only supports the new controller pins via the Web UI. It will take a while to update the INDI driver. I haven't tried the TCP API but it should work. Web Sockets API will definitely take some additional work. I may decide to drop it. Usual upgrade instructions should work.

hcomet, 2025-02-13:
Its just what I called the GitHub branch that I'm making my changes in (typo -  should be CheapoDC-Plus) . Once I'm done I'll merge that branch back into the main branch where I do the releases from. Since the changes will be fairly big and include both code and documentation its easier to work in a separate branch without impacting the main branch. So far I've only made the code changes. Lots of other things to do but the main code seems to be working. You can set up 4 additional pins to be tied to the main Dew Controller pins (Controller mode) or independent and using their own PWM (PWM mode) or just On/Off (Boolean mode). Default is that they are Disabled.

In the Device Management Web UI you'll need to pic a GPIO pin first, Update. Then pick an output mode, Update. Then depending on the mode you can adjust the output.

The link to the zip file will download everything in that branch similar to when you get a zip for the latest release. You can wait for me to finish the full release or you can give it a try now.

It should be backwards compatible with the current driver in INDI/Stellarmate. The two main outputs will work but you won't be able to control the additional outputs via INDI/Stellarmate. Given the release schedule for INDIlib the next release there is likely April so assuming I can get into that release it will be April before a new driver gets picked up.

Thanks for the Stellarmate request.

LordWhiteley-UK, 2025-02-13:
Are you saying then that you could say connect 4 additional MOSFET switches, so that you could have 4 on/off DC ports or PWA or a combination of both??

If my assumption is correct, do you recommend 4 ESP32 pins to use  - there’s 12 GPIO ports on the ESP32 C3 Mini (with the first two controlling the two dew heaters).

Luckily, I haven’t sent off the PCB yet as I want to double check another PCB design I have for a two stepper OnStep controller for the DIY Harmonic Drive EQ mount I designed :)

hcomet, 2025-02-13:
Yes, you could use 4 additional MOSFET switches. You can actually redefine any of the 6 outputs to connect to whatever GPIO pins you want. The software/UI  refers to the pins as Controller Pin 0 through Pin 5. Both Pin 0 and Pin 1 may be disabled or Controller mode pins. You can leave them where they are currently connected (I used GPIO 0 and 1). Pin 2 through 5 can where you want but you which GPIO you pick is dependent on the ESP32-C3 module you are using.

I think you are using the same one I've been using which is the ESP32-C3 Super Mini. Check out the schematic here: [https://michiel.vanderwulp.be/domotica/Modules/ESP32-C3-SuperMini/](https://michiel.vanderwulp.be/domotica/Modules/ESP32-C3-SuperMini/).

You'll see that GPIO 0, 1, 3, 4, 5, 7, 10, 20, 21 look to be free.
GPIO2 has a pull up resistor on it.
GPIO6 is set up as an RTC oscillator of some sort.
GPIO8 is the status Led
GPIO9 is the Boot button.

I've tested with GPIOs 0, 1, 3, 4, 5 and 7 so far without issues.

hcomet, 2025-02-13:
Actually not using A2 so not A0 to A5. A2 can be used but it will be pulled-up until software takes over and sets it to zero after boot.

LordWhiteley-UK, 2025-02-13:
Ok noted, so A0 & A1 as before, then A3, A4, A5 and A7 ?

hcomet, 2025-02-13:
You got it.

Good luck,

Closed 2025-03-21.

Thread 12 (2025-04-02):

Outputs not switching with latest firmware 2.2.0??

LordWhiteley-UK, 2025-04-02:
OK, so I have now received the two PCB's I designed.

One for the original dew controller & and the other one with the 4 switched outputs. Assembled them both and flashed to the latest firmware 2.2.0

The first PCB works perfectly and you can manually turn (ie set to ON and 100%)
on the two dew controllers and so that's all working perfectly.

However, when I connected the second PCB, non of the switched outputs worked.

I initially set Controller Output 2 to GPIO 2 & Update - noticing that you sometimes get a whirling circle on the webpage because something is taking too long to respond??

I then set to Controller mode and ensured on the dew controller page that 100% was set, the dew controllers come
on but non of the outputs and probing GPIO 3,4,5 & 7 are all LOW

NB GPIO2 seems high to be high all the time?

So I'm sure if I've done something wrong or that there is a bug somewhere in the firmware?

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

hcomet, 2025-04-02:
I don't think GPIO2 was one of the GPIOs that I recommended to use. If you look at the ESP32-C3 SuperMini schematic its tied high with a 10K resistor. You can use it but it will start off high on boot.

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

I'm not sure why you're having an issue with the other GPIOs. I'd say to test it with the ESP32-C3 module free of the boards but I see its soldered down. Any chance there's a short pulling them down?

I have used 2.2.0 on several different ESP32-C3 modules without issue.

LordWhiteley-UK, 2025-04-02:
Ok so GPIO is supposed to be high, just something I noticed.
As I said I did monitor GPIO 3,4,5 & 7 and they all remained LOW.
I do have another ESP32 in my second dew controller, so I’ll program that and check the outputs.
However, the mosfet circuits on the second PCB are exactly the same as those on the first PCB which works perfectly.
I did notice that if turned on the dew heaters to 100% and then set controller output 2 to GPIO 3 and controller mode and set 100% - the MOSFET circuit remained off and it turned off the dew outputs?
Anyway, I’ll check the other ESP32 C3 that I have…

hcomet, 2025-04-02:
An idea for checking your board versus the firmware. Try flashing your board with something simpler to test the GPIOs. You could modify the Blink example code to blink all of the GPIOs that you use and then test them to see if they are switching from low to high to low etc...

The Web UI seems to have a random timing issue. It send s off the command for whatever change you input and then commands for updating all the fields in UI. They are all sent asynchronously with a queue waiting for the responses. If a response is missed then it will sit with the waiting spinner running forever. If it seems stuck then just refresh the page. I think the issue is with getting all the responses not with sending the update so a page refresh should fix it.

hcomet, 2025-04-02:
Okay, I have a test unit that I put together which uses 6 dual MOSFETs for 6 outputs. The simplest test using the firmware is to configure them all the same as Controller outputs.

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

Then set the Controller Mode to Manual:

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

Then manually modify the Controller Output to change all of the outputs. Here's a video that steps them up from 0% to 100% and back down to 0% by 25% increments. The LEDs are connected to the MOSFET outputs so I know they are working. Outputs 0 and 1 are on the backside. The LED on top is plugged into output 0. 2 through 5 are on the front. If you turn up the sound you can hear me type in the new value and then the mouse click each time I change the output.

https://github.com/user-attachments/assets/fc739b06-1335-468f-812e-05b1f700e6ac

hcomet, 2025-04-03:
That should be doable through the Device Management UI. Just leave the two outputs as Controller mode and then set the other four to Boolean mode. Then the four Boolean mode outputs are independently switchable to either 0% or 100%. Really, they are either On or Off since the outputs are switched to be digital outputs not PWM outputs.

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

If you are using the outputs to control something like a computer then you definitely want them set to Boolean. You do not want a PWM signal going to something dependent on a flat DC output. That could accidentally happen with Controller or PWM mode. Boolean mode can only be fully On or Off. Even if you wrote code to send an API command to set a Boolean mode output to something less than 100% it will only switch fully On.

BTW: the updated INDI driver is also available in the latest version released earlier this week: [https://github.com/indilib/indi/releases/tag/v2.1.3](https://github.com/indilib/indi/releases/tag/v2.1.3) on GitHub. I assumed you used StellarMate but I don't know how long it will take for a StellarMate update to come out. But, then you can also control the four outputs through the StellarMate driver, on the main control tab. This just shows the four outputs can be independently Controller, PWM or Boolean.

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

The latest INDI documentation for CheapoDC can be found [here](https://hcomet.github.io/CheapoDC/indi/CheapoDC.html).

LordWhiteley-UK, 2025-04-10:
Yes, it can :)
I've just sent off a new single PCB (components fitted both sides) and I am in the process of designing a 3D enclosure for it. I'll do a write up and post it somewhere???

hcomet, 2025-04-10:
I'm also finishing up a write-up with cases for a 3 output and 6 output build. Both use the off the shelf modules. I'll be posting the write-up on my GitHub Pages which provides web hosting: [https://hcomet.github.io/](https://hcomet.github.io/). If you go to [https://pages.github.com/](https://pages.github.com/) you can set your own up. You'll need to know how to do HTML etc... to post anything though.

The alternative is to create a repository for it on your GitHub and put everything there. You can do the write-up in markdown which is easier to learn. Your schematics, pcb files and 3d files can all go there.

In either case, the schematics, pcb files and 3d files should all go in a repository. The write-up goes where you're most comfortable doing it.

I have know problem referencing it from my site once your done. Just let me know.

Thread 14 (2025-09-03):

Temperature and humidity sensor probe

odkmo, 2025-09-03:
I was curious if there was a way to connect a temperature and humidity sensor directly to the board and use these inputs to bypass the need for WiFi?

hcomet, 2025-09-03:
I assume you mean internet more than WiFi. The primary UI and API are only available via WiFi and that cannot be changed.

Currently support for a locally connected temperature and humidity sensor is not supported. That was not the original intent of the the project. But, then again, support for up to 6 outputs was also not part of the original intent. There is development work required to add support for a temperature/humidity sensor to the CheapoDC and unfortunately I'm in the middle of another project. It may take me a couple of months to get to adding this. Also already pushing the boundary of the usable pins on the ESP32-C3 supermini board, so will need to confirm I can physically add a sensor.

If you need a solution now then there are a few other dew controller projects out there. I've built [Robert Brown's ESP32 Dew Controller](https://sourceforge.net/projects/esp32-dew-controller/). It works well although a bit more complicated and involved to build.

Thanks.

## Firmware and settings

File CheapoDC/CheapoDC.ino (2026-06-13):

// ******************************************************************
// CheapoDC main
// Cheap and easy Dew Controller
// Details at https://github.com/hcomet/CheapoDC
// (c) Copyright Stephen Hillier 2024. All Rights Reserved.
// ******************************************************************

#include <Arduino.h>
#include <TimeLib.h>
#include "CDCdefines.h"
#include "CDCEasyLogger.h"
#include "CDCWebSrvr.h"
#include "CDCvars.h"
#include "CDCSetup.h"
#if defined(CDC_ENABLE_CMDQUEUE) || defined(CDC_ENABLE_WEB_SOCKETS)
#include "CDCommands.h"
#endif

char programName[] = "CheapoDC"; // Program name
char programVersion[] = "2.3.1";  // program version

CDCSetup *theSetup; // main setup class
dewController *theDController;

// Counters used for time based scheduler in main loop
int milliCount = 0;
unsigned long milliLast = 0;
unsigned long milliDelta = 0;
int secCount = 0;
unsigned int secLast = 0;
unsigned int secDelta = 0;
int minCount = 0;
unsigned int minLast = 0;
unsigned int minDelta = 0;

// Counters for items scheduled
//
// Status LED timer in milliseconds
int statusLEDDelta = 0;
int statusLEDLast = 0;
int statusLEDCountDown = CDC_STATUS_LED_DELAY;

#if defined(CDC_ENABLE_CMDQUEUE) || defined(CDC_ENABLE_WEB_SOCKETS)
// run command queue timer in msec only for Web Sockets enabled
int runCmdQueueDelta = 0;
int runCmdQueueLast = 0;
#endif
// Weather query timer in minutes
int weatherQueryDelta = 0;
int weatherQueryLast = 0;
// Controller Output update timer in minutes
int controllerUpdateDelta = 0;
int controllerUpdateLast = 0;
// Save configuration check in seconds
int saveConfigDelta = 0;
int saveConfigLast = 0;
// Humidity Sensor scan timer in minutes
int humiditySensorDelta = 0;
int humiditySensorLast = 0;

// Timer functions for scheduled services
void ledTimer(int timeCheck)
{

  if (theSetup->getStatusBlinkEvery() != 0)
  {
    if ((timeCheck - statusLEDLast) < 0)
    {
      statusLEDDelta = 1000 - statusLEDLast + timeCheck;
    }
    else
    {
      statusLEDDelta = timeCheck - statusLEDLast;
    }

    if (statusLEDDelta >= theSetup->getStatusBlinkEvery())
    {
      theSetup->blinkStatusLED();
      statusLEDDelta = 0;
      statusLEDLast = timeCheck;
    }
  }
}

#if defined(CDC_ENABLE_CMDQUEUE) || defined(CDC_ENABLE_WEB_SOCKETS)
void runCmdQueueTimer(int timeCheck)
{

    if ((timeCheck - runCmdQueueLast) < 0)
    {
      runCmdQueueDelta = 1000 - runCmdQueueLast + timeCheck;
    }
    else
    {
      runCmdQueueDelta = timeCheck - runCmdQueueLast;
    }

    if (runCmdQueueDelta >= CDC_RUNCMDQUEUE_EVERY)
    {
      runCmdPostProcessQueue();
      runCmdQueueLast = timeCheck;
    }
}
#endif

void weatherQueryTimer(int timeCheck)
{

  if (theSetup->getWeatherQueryEvery() != 0)
  {
    if ((timeCheck - weatherQueryLast) < 0)
    {
      weatherQueryDelta = 60 - weatherQueryLast + timeCheck;
    }
    else
    {
      weatherQueryDelta = timeCheck - weatherQueryLast;
    }

    if (weatherQueryDelta >= theSetup->getWeatherQueryEvery())
    {
      theSetup->queryWeather();
      weatherQueryLast = timeCheck;
    }
  }
}

void controllerUpdateTimer(int timeCheck)
{
  if (theSetup->getControllerUpdateEvery() != 0)
  {
    if ((timeCheck - controllerUpdateLast) < 0)
    {
      controllerUpdateDelta = 60 - controllerUpdateLast + timeCheck;
    }
    else
    {
      controllerUpdateDelta = timeCheck - controllerUpdateLast;
    }

    if (controllerUpdateDelta >= theSetup->getControllerUpdateEvery())
    {
      LOG_DEBUG("controllerUpdateTimer", "Call update output" << theSetup->getDateTime());
      theDController->updateOutput();
      controllerUpdateLast = timeCheck;
    }
  }
}

void saveConfigTimer(int timeCheck)
{
  if ((timeCheck - saveConfigLast) < 0)
  {
    saveConfigDelta = 60 - saveConfigLast + timeCheck;
  }
  else
  {
    saveConfigDelta = timeCheck - saveConfigLast;
  }

  if (saveConfigDelta >= CDC_DEFAULT_SAVE_CONFIG_EVERY)
  {
    // Update config file too
    saveConfigLast = timeCheck;
    if (!theSetup->SaveConfig())
    {
      LOG_ALERT("saveConfigTimer", "Failure to save config file");
    }
  }
}

void humiditySensorTimer(int timeCheck)
{

  if (theSetup->checkHumiditySensor())
  {
    if ((timeCheck - humiditySensorLast) < 0)
    {
      humiditySensorDelta = 60 - humiditySensorLast + timeCheck;
    }
    else
    {
      humiditySensorDelta = timeCheck - humiditySensorLast;
    }

    if (humiditySensorDelta >= 2)
    {
      if (!theSetup->updateSensorReadings())
      {
        LOG_ALERT("humiditySensorTimer", "Failure to update Humidity Sensor readings.");
      }
      humiditySensorLast = timeCheck;
    }
  }
}

// Main setup
void setup()
{

  sleep(1);
  Serial.begin(115200);
  sleep(1);
  LOG_ALERT("setup","Initializing " << programName << ". FW: " << programVersion);

  theDController = new dewController();
  theSetup = new CDCSetup();
  
  LOG_DEBUG("Main-setup", "Load CheapoDC configuration");
  if (!theSetup->LoadConfig())
  {
    LOG_ERROR("Main-setup", "Load Configuration Failure. Will continue on defaults.");
  }

  // initialize status LED
  theSetup->blinkStatusLEDEvery(CDC_DEFAULT_STATUS_BLINK);
  theSetup->statusLEDOn();

  LOG_DEBUG("Main-setup", "Setup WiFi");
  if (!theSetup->setupWiFi())
  {
    LOG_ERROR("Main-setup", "Wifi connection failure");
  }

  if (theSetup->getInWiFiAPMode())
  {
    theDController->setControllerMode(OFF);
  }

  if (theSetup->setupHumiditySensor())
  {
    LOG_ALERT("Main-setup", "Humidity sensor found and configured.");
  }
  else
  {
    LOG_ALERT("Main-setup", "Humidity sensor not found.")
  }
  
  // Adjust Timezone etc....
  configTime(theSetup->getLocation().timezone, theSetup->getLocation().DSTOffset, theSetup->getNTPServerURL());
  now();
  

  #if LOG_LEVEL == LOG_LEVEL_DEBUG
  struct tm lTime;
  getLocalTime(&lTime);
  LOG_DEBUG("Main-setup", "Local time struct: ");
  LOG_DEBUG("Main-setup", "  seconds: " << lTime.tm_sec);
  LOG_DEBUG("Main-setup", "  minutes: " << lTime.tm_min);
  LOG_DEBUG("Main-setup", "  hours: " << lTime.tm_hour);
  LOG_DEBUG("Main-setup", "  m-day: " << lTime.tm_mday);
  LOG_DEBUG("Main-setup", "  month: " << lTime.tm_mon);
  LOG_DEBUG("Main-setup", "  year: " << lTime.tm_year);
  LOG_DEBUG("Main-setup", "  y-day: " << lTime.tm_yday);
  LOG_DEBUG("Main-setup", "  is DST: " << lTime.tm_isdst);
  #endif

  setupServers();

  theSetup->statusLEDDelay( RESET_DELAY );
  LOG_DEBUG("CDCSETUP", "Weather query every: " << theSetup->getWeatherQueryEvery());
  // Synchronize with RTC for scheduling
  milliLast = millis();
  secCount = theSetup->getSecond();
  minCount = theSetup->getMinute();

  // Enable and make first weather query
  theSetup->setWeatherQueryEnabled( true );
  if (theSetup->getWeatherQueryEvery() != 0)
  {
    theSetup->queryWeather();
    weatherQueryLast = minCount;
  }

  theDController->setEnabled();
  #if defined(CDC_ENABLE_CMDQUEUE) || defined(CDC_ENABLE_WEB_SOCKETS)
  clearCmdPostProcessQueue();
  #endif
}

// Main loop
void loop()
{
  // put your main code here, to run repeatedly:
  milliDelta = millis() - milliLast;
  if (milliDelta > 0)
  { // Only do things if loop >= 1 millisec
    milliCount = milliCount + milliDelta;
    milliLast = millis();

    // Set up elapsed millisec, sec, minutes
    if (milliCount >= 1000)
    {
      milliCount = 0;
      secCount++;
      if (secCount >= 60)
      {
        secCount = 0;
        minCount++;
        if (minCount >= 60)
          minCount = 0;
      }
    }

    // Do millisec timer items
    ledTimer(milliCount);
#if defined(CDC_ENABLE_CMDQUEUE) || defined(CDC_ENABLE_WEB_SOCKETS)
    runCmdQueueTimer(milliCount);
#endif
    // End milliseconds check

    // Do seconds timer items
    if ((secCount - secLast) != 0)
    {
      secLast = secCount;
      
      theSetup->statusLEDDelay( DEC_DELAY );

      // call save config file timer
      saveConfigTimer(secCount);
      // Check for ask to do HTTP OTA Update
#ifdef CDC_ENABLE_HTTP_OTA
      updateFirmware();
#endif
      // End Seconds check

      // Do minute timer items
      if ((minCount - minLast) != 0)
      {
        minLast = minCount;

        // call weather query timer
        weatherQueryTimer(minCount);

        // call update controller timer
        controllerUpdateTimer(minCount);

        // call update humidity sensor readings
        humiditySensorTimer(minCount);

      } // End Minutes check
    }
  }
}

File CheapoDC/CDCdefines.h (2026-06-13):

// *************************************************************************************
// CheapoDC defines
// Cheap and easy Dew Controller
// (c) Copyright Stephen Hillier 2024. All Rights Reserved.
// *************************************************************************************
// Before building configure the following in the defines below:
// 1 - Configure the PWM pins as appropriate for your ESP32
// 2 - Enable Basic Web Authentication and change the ID/Password
// 3 - Configure Network settings for WiFI (Can also be done through CDCWiFi,json file )
// 4 - Set up a free OpenWeather API account and get an API Key
//
// Almost everything else has defaults that should be left alone and then configuration
// done through the Web based Configuration UI. http://cheapo.local/config
// *************************************************************************************
//
#ifndef MY_CDCDEFINES_H
#define MY_CDCDEFINES_H

#include <Arduino.h>

// *************************************************************************************
// ESP32 C3 Board configuration defaults
// *************************************************************************************
#define CDC_DEFAULT_CONTROLLER_PIN0 0  // set first Controller output default
#define CDC_DEFAULT_CONTROLLER_PIN1 1  // set second Controller output default
#define CDC_CONTROLLER_PWM_CHANNEL 0      // The PWM Channel used for Dew Controller managed Pins (Don't change)
#define CDC_PIN_NOT_CONFIGURED -1  // Used to indicate that a pin has not been configured

// *************************************************************************************
// Builtin LED or other pin to use for Status LED.
// Status LED is used to show WiFi mode and config changes via blinks
// 1 second blink (500ms on/500ms off) is successful Station Mode - CDC_DEFAULT_STATUS_BLINK
// 0.2 second blink (100ms on/100ms off) is fall back to Access Point Mode - CDC_WIFI_AP_STATUS_BLINK
// Blink will continue for 10 seconds then turn off - CDC_STATUS_LED_DELAY
// *************************************************************************************
#define CDC_DEFAULT_STATUS_LED_PIN 8                      // Pin to use for Status LED
#define CDC_DEFAULT_STATUS_BLINK 500          // every x millisec
#define CDC_WIFI_AP_STATUS_BLINK 100          // every x millisec
#define CDC_STATUS_LED_DELAY 10               // time until status LED is turned off in seconds (0 = infinite delay)
#define CDC_STATUS_LED_BLINK_ON_CONFIG_CHANGE // Blink for delay time when config item changed
#define CDC_STATUS_LED_BLINK_ON_POWER_CHANGE  // Blink for delay time when Power Output changes
//#define CDC_REVERSE_HIGH_LOW                // Some ESP32-C3 seem to have onboard LEDs with High/Low reversed. Uncomment to reverse.
#ifdef CDC_REVERSE_HIGH_LOW
#define CDC_STATUS_LED_HIGH LOW
#define CDC_STATUS_LED_LOW HIGH
#else
#define CDC_STATUS_LED_HIGH HIGH
#define CDC_STATUS_LED_LOW LOW
#endif

// *************************************************************************************
// Network configuration
// *************************************************************************************
#define CDC_DEFAULT_HOSTNAME "cheapodc"             // default hostname. Can also be set in CDCWiFi.json
#define CDC_DEFAULT_WIFI_SSID "defaultSSID"         // default SSID for STA mode. Can also be set in CDCWiFi.json
#define CDC_DEFAULT_WIFI_PASSWORD "defaultPassword" // default WiFi Password. Can also be set in CDCWiFi.json
#define CDC_DEFAULT_WIFI_AP_PASSWORD "cheapodc"     // WiFi password for AP mode
#define CDC_DEFAULT_WIFI_CONNECTATTEMPTS 10         // Number of times to try to connect to an AP when in STA mode
#define CDC_DEFAULT_WIFI_TRYAPS 1                   // Number of times to cycle through APs when in STA mode
//#define CDC_ENABLE_WIFI_TX_POWER_MOD WIFI_POWER_8_5dBm // Uncomment to adjust WiFi TX power if you are having connection issues

// *************************************************************************************
// *************************************************************************************
// ***********         DO NOT change anything below here.                    ***********
// *************************************************************************************
// *************************************************************************************
// Defaults for Web Authentication
#define CDC_DEFAULT_WEB_ID "admin"       // Change to change logon ID
#define CDC_DEFAULT_WEB_PASSWORD "admin" // Change to change logon password
#define CDC_DEFAULT_WEB_REALM "CheapoDC" // Change to change logon realm
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

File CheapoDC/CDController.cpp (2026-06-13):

// ******************************************************************
// CheapoDC Dew Controller configuration and management
// Cheap and easy Dew Controller
// Details at https://github.com/hcomet/CheapoDC
// (c) Copyright Stephen Hillier 2024. All Rights Reserved.
// ******************************************************************

#include <Arduino.h>
#include <ArduinoJson.h>
#include "CDCdefines.h"
#include "CDCEasyLogger.h"
#include "CDCvars.h"
#include "CDCSetup.h"
#include "CDController.h"

dewController::dewController(void)
{
    // Initialize all Controller Outputs as disabled
    LOG_DEBUG("dewController", "Setup and configure dew controller PWM outputs");
    for (int i = 0; i < MAX_CONTROLLER_PINS; i++)
    {
        this->_controllerPinSettings[i].controllerPinPin = CDC_PIN_NOT_CONFIGURED;
        this->_controllerPinSettings[i].controllerPinMode = CONTROLLER_PIN_MODE_DISABLED;
        this->_controllerPinSettings[i].controllerPinOutput = 0;
    }

    // If defaults set in CDCdefines.h for PIN0 and PIN1 then configure
#ifdef CDC_DEFAULT_CONTROLLER_PIN0 
    LOG_DEBUG("dewController", "Controller Output 0: " << CDC_DEFAULT_CONTROLLER_PIN0);
  
    this->_controllerPinSettings[CONTROLLER_PIN0].controllerPinPin = CDC_DEFAULT_CONTROLLER_PIN0;
    this->_controllerPinSettings[CONTROLLER_PIN0].controllerPinMode = CONTROLLER_PIN_MODE_CONTROLLER;
#endif // CDC_DEFAULT_CONTROLLER_PIN0
#ifdef CDC_DEFAULT_CONTROLLER_PIN1
    LOG_DEBUG("dewController", "Controller Pin 1: " << CDC_DEFAULT_CONTROLLER_PIN1);

    this->_controllerPinSettings[CONTROLLER_PIN1].controllerPinPin = CDC_DEFAULT_CONTROLLER_PIN1;
    this->_controllerPinSettings[CONTROLLER_PIN1].controllerPinMode = CONTROLLER_PIN_MODE_CONTROLLER;
#endif // CDC_DEFAULT_CONTROLLER_PIN1

    this->_currentControllerMode = CDC_DEFAULT_CONTROLLER_MODE;
    this->_currentTemperatureMode = CDC_DEFAULT_TEMPERATURE_MODE;
    this->_currentSetPointMode = CDC_DEFAULT_SET_POINT_MODE;
    this->_currentOutput = CDC_MINIMUM_CONTROLLER_OUTPUT;
    this->_currentTemperatureSetPoint = CDC_DEFAULT_TEMPERATURE_SET_POINT;
    this->_currentTrackPointOffset = CDC_DEFAULT_TRACK_POINT_OFFSET;
    this->_currentTrackingRange = CDC_DEFAULT_TRACKING_RANGE;
    this->_currentTrackPoint = 0.0;
    this->_minimumOutputSetting = CDC_MINIMUM_CONTROLLER_OUTPUT;
    this->_maximumOutputSetting = CDC_MAXIMUM_CONTROLLER_OUTPUT;
    this->_controllerEnabled = false;
}

bool dewController::setEnabled()
{
    this->_controllerEnabled = true;
    LOG_DEBUG("setEnabled", "Controller enabled");
    // Enable all configured Pins
    for (int i = CONTROLLER_PIN0; i < MAX_CONTROLLER_PINS; i++)
    {
        if (this->_controllerPinSettings[i].controllerPinPin != CDC_PIN_NOT_CONFIGURED) {
            if(!this->setControllerPinMode(i, this->_controllerPinSettings[i].controllerPinMode)) {
                LOG_ERROR("setEnabled", "Controller Output failure " << i << ". Controller cannot be enabled.");
                this->_controllerEnabled = false;
                return false;
            }
        }
    }
    this->updateOutput();
    return true;
}

bool dewController::setControllerPinPin(int controllerPin, int pin)
{
    if ((controllerPin < CONTROLLER_PIN0) || (controllerPin > CONTROLLER_PIN5))
    {
        LOG_ERROR("setControllerPinPin", "Invalid controller output value: " << controllerPin);
        return false;
    }

    if (pin == -1) {
      this->setControllerPinMode( controllerPin, CONTROLLER_PIN_MODE_DISABLED);
      return true;
    }

    if ((pin < 0) || (pin > 39))
    {
        LOG_ERROR("setControllerPinPin", "Invalid pin number: " << pin);
        return false;
    }

    if (pin == theSetup->getStatusLEDPin())
    {
      LOG_ERROR("setControllerPinPin", "Cannot set Controller Output " << controllerPin << " to same as LED Status Pin: " << pin);
      return false;
    }

    for (int i = 0; i < MAX_CONTROLLER_PINS; i++)
    {
        if ((this->_controllerPinSettings[i].controllerPinPin == pin) && (i != controllerPin))
        {
            LOG_ERROR("setControllerPinPin", "Pin " << pin << " already assigned to controller output " << i);
            return false;
        }
    }

    if ((this->_controllerEnabled) && ((this->_controllerPinSettings[controllerPin].controllerPinMode != CONTROLLER_PIN_MODE_DISABLED) || 
        (this->_controllerPinSettings[controllerPin].controllerPinPin != CDC_PIN_NOT_CONFIGURED)))
    {
        if (!this->setControllerPinMode(controllerPin, CONTROLLER_PIN_MODE_DISABLED)) {
            LOG_ERROR("setControllerPinPin", "Controller Output " << controllerPin << " is enabled. Pin cannot be changed.");
            return false;
        }
    }

    this->_controllerPinSettings[controllerPin].controllerPinPin = pin;
    LOG_DEBUG("setControllerPinPin", "Controller Output " << controllerPin << " set to: " << pin);
    return true;
}
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

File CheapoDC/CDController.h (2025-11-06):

// ******************************************************************
// CheapoDC Dew Controller configuration and management
// Cheap and easy Dew Controller
// Details at https://github.com/hcomet/CheapoDC
// (c) Copyright Stephen Hillier 2024. All Rights Reserved.
// ******************************************************************
#ifndef MY_CDCONTROLLER_H
#define MY_CDCONTROLLER_H

#include <Arduino.h>
#include "CDCdefines.h"
#include "CDCvars.h"

#define CDC_CONTROLLERMODE_JSONARRAY "{\"Mode\":[\"Automatic\",\"Manual\",\"Off\"]}"
enum controllerMode
{
        AUTOMATIC, // 0
        MANUAL,    // 1
        OFF        // 2
};

#define CDC_TEMPERATUREMODE_JSONARRAY "{\"Mode\":[\"Weather Source\",\"External Input\"]}"
enum temperatureMode
{
        WEATHER_QUERY, // 0
        EXTERNAL_INPUT // 1
};

#define CDC_SETPOINTMODE_JSONARRAY "{\"Mode\":[\"Dew Point\",\"Temperature\",\"Midpoint\"]}"
enum setPointMode
{
        DEWPOINT,    // 0
        TEMPERATURE, // 1
        MIDPOINT     // 2
};

enum controllerPinNumber
{
        CONTROLLER_PIN0 = 0,    // 0
        CONTROLLER_PIN1,        // 1
        CONTROLLER_PIN2,        // 2
        CONTROLLER_PIN3,        // 3
        CONTROLLER_PIN4,        // 4
        CONTROLLER_PIN5,        // 5
        MAX_CONTROLLER_PINS     // 6
};

#define CDC_PIN_MODE_JSONARRAY "{\"Mode\":[\"Disabled\",\"Controller\",\"PWM\",\"Boolean\"]}"
enum controllerPinModes
{
        CONTROLLER_PIN_MODE_DISABLED = 0,       // 0
        CONTROLLER_PIN_MODE_CONTROLLER,         // 1
        CONTROLLER_PIN_MODE_PWM,                // 2
        CONTROLLER_PIN_MODE_BOOLEAN             // 3
};

struct controllerPinSetting
{
        int controllerPinPin;
        controllerPinModes controllerPinMode;
        int controllerPinOutput;
};

class dewController
{
public:
        dewController(void);
        void updateOutput(int output = -1); // Controller mode outputs only
        bool setControllerPinPin(int controllerPin, int pin );
        bool setControllerPinMode(int controllerPin, controllerPinModes mode);
        bool setControllerPinOutput(int controllerPin, int output);
        int getControllerPinPin(int controllerPin);
        controllerPinModes getControllerPinMode(int controllerPin);
        int getControllerPinOutput(int controllerPin);

        void setControllerMode(controllerMode mode);
        void setTemperatureMode(temperatureMode mode);
        void setSetPointMode(setPointMode mode);
        void setSetPoint(float setPointTemperature);
        void setTrackPointOffset(float trackPointOffset);
        void setTrackingRange(float trackingRange);

        void setMinOutput(int output);
        void setMaxOutput(int output);
        bool setEnabled();
        void setDisabled() { this->_controllerEnabled = false; };

        int getOutput() { return this->_currentOutput; };
        int getMinOutput() { return this->_minimumOutputSetting; };
        int getMaxOutput() { return this->_maximumOutputSetting; };
        controllerMode getControllerMode(void) { return this->_currentControllerMode; };
        temperatureMode getTemperatureMode(void) { return this->_currentTemperatureMode; };
        setPointMode getSetPointMode(void) { return this->_currentSetPointMode; };
        float getSetPoint(void) { return this->_currentTemperatureSetPoint; };
        float getTrackPointOffset(void) { return this->_currentTrackPointOffset; };
        float getTrackPoint(void) { return this->_currentTrackPoint; }
        float getTrackingRange(void) { return this->_currentTrackingRange; };

private:
        controllerMode _currentControllerMode;
        temperatureMode _currentTemperatureMode;
        setPointMode _currentSetPointMode;
        int _currentOutput;
        float _currentTemperatureSetPoint;
        float _currentTrackPointOffset;
        float _currentTrackingRange;
        float _currentTrackPoint;
        int _minimumOutputSetting;
        int _maximumOutputSetting;
        bool _controllerEnabled;

        int _calculateOutput(float currentTemperature, float setPoint, float range, float offset);
        controllerPinSetting _controllerPinSettings[MAX_CONTROLLER_PINS];
};

#endif

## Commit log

2024-02-22 Fix a couple of images.
2024-03-09 Cleanup and fixes after testing with INDI driver.
    [CDCSetup.cpp, CDCSetup.h, CDCdefines.h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]
2024-03-13 Fix root Web UI page to process template variables.
    [CheapoDC.ino]
2024-07-15 Updating build documentation to clarify IDE versions, Espressif version and other libraries. Also clarify use of LittleFS. Close Cannot bring up webpages loaded on ESP32 #1
2024-07-16 Update documentation and fix MOSFET connections in wiring diagram.
2024-07-25 Fix OpenWeather API string in CDCdefines.h to add units paramterr for metric results. Fixes OpenWeather API string not set to Metric units properly #2. Also some documentation typo fixes.
    [CDCdefines.h]
2024-10-29 Version 2.0 Initial push
    V2.0 Update for:
    - ESP32 Espressif 3.x library support
    - ArduinoJSON 7.x support
    - External weather station support
    - INDI driver update to support weather devices
2024-10-29 Delete CheapoDC/build/esp32.esp32.lolin_s3_mini directory
    Remove extra files sucked up in commit...
2024-11-04 Update indilib.org listing details and images. Bug fixes to CheapoDC firmware and documentation updates.
    [CDCSetup.cpp, CDCSetup.h, CDCdefines.h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]
2024-11-04 Delete CheapoDC/build/esp32.esp32.lolin_s3_mini directory
    Remove extra build folder.
2024-11-05 Clean up and Fixes
    Documentation clean up and hopefully final fixes before closing off the V2.0.0 rlease.
    [CDCSetup.cpp, CDCdefines.h, CDController.cpp]
2025-01-18 PWM Output always Zero
    PWM always set to zero. Found in issue #4
    [CDController.cpp]
2025-01-18 Update release number for fix
    Change release string to 2.0.1
    [CheapoDC.ino]
2025-01-18 PWM on Pin2 not working
    Fix issue #5
    [CDController.cpp]
2025-01-18 Update version and add error checking
    Update to version 2.0.2 and add error checking for PWM channel attach.
    [CDController.cpp, CheapoDC.ino]
2025-01-19 Add option to set WiFi TX power
    Some people are having issues with ESP32-C4 connecting to WiFi. Setting TX power to 8.5dbm solves this for those with the issue. Now optionally settable in CDCdefines.h.
    [CDCSetup.cpp, CDCdefines.h]
2025-01-20 Update build instructions
    Add info for setting WiFi TX power and comment on ESPAsyncWebServer issues with ESP Arduino Core 3.1.x.
2025-01-20 Switch ESPAsyncWebServer libraries
    Changes to support ESP32 Asynchronous Networking ESPAsyncWebServerr v3.6.0
2025-01-20 Add ESP32Async library info to README.md
    Update Build information in README for switch to ESP32Async versions of the webserver and tcp libraries.
2025-01-23 Fix Download file
    Complete work for part 1 of #6
    Moving to ESPAsync version of ESPAsynWebServer broke the download file implementation in CheapoDC. Fixed in this commit.
    [CDCommands.cpp]
2025-01-24 Support Minimal SPIFFS partition scheme
    Work for issue #6
    - Create Data Source to hold editable HTML, CSS, JS files
    - Minimize/compress all HTML, CSS, JS, PNG for Sketch Data folder
    - Update documentation for move to new partition scheme
    [CDCSetup.cpp]
2025-02-11 Improve runtime configuration capability
    Move controller pin to runtime configuration from compile time - #10
    Add additional pins that may be controlled by CheapoDC - #9
    - 4 addtional pins added
    - each may be set up as:
    - Disabled
    - Controller attached with 2 dew controller pins
    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
2025-02-26 Additional device confoguration
    Allow for complete device configuration at runtime using Device Management Web UI, support for #10 :
    - add password change
    - add Status LED configuration
    - cleanup Controller Pin configuration
    Deprecate WebSocket API
    - remove WebSocket based config page from Web UI
    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
2025-03-05 Continued CheapoDC Plus work
    Allow install & upgrade without Arduino IDE
    - support for Web based HTTP OTA of both FW and Data partitions
    - support config backup/restore during data partition OTA upgrade
    - add Web HTTP OTA update to Web UI
    - add password change support to Web UI
    - add Status LED pin setup to Web UI
    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
2025-03-14 More CheapoDC-Plus work
    - add ability to update hostname to Web UI
    - merge javascript into single file so it can be minimized
    - shorten CSS class names and custom tags to save data partition space
    - fix issue with event listeners being created over and over....
    - update documentation
    [CDCSetup.cpp, CDCdefines.h, CDCommands.cpp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]
2025-03-19 Clean up Web OTA Update
    - Add verified HTTPS support for HTTP OTA
    - support root CA override
    - minor fixes and documentation updates
    [CDCSetup.cpp, CDCdefines.h]
2025-05-24 Add 3D Models
    Adding 3D model files for the 3-Output and 6-Output build versions.
    [3-output-bottom.stl, 3-output-case.3mf, 3-output-output-panel.stl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]
2025-05-30 Fix image links from indilib.org
    Restore the images that are linked to from the INDI driver description on indilib.org.
2025-10-27 Support testing of new INDI driver
    Add in the basic structure, commands and response to support new Internal Source mode for Weather Source.
    Allow setting SDA and SCL pins for humidity sensor.
    TO DO: Humidity Sensor support.
2025-11-02 #14 Temperature and Humidity Probe
    New feature added for #14 request for internal humidity/temperature sensor.
    Support for internal SHT3X Humidity sensor added. Pins 9 & 10 used for SCL and SDA.
    Works when Weather Source set to Internal Source.
    TODO: Documentation, WebUI and additional QA. Then WebFlash and upgrade Flash.
2025-11-03 Update main README.md
    Add humidity sensor information to main README.md
    Minor code cleanup
    switch to using "Weather Source" instead of "Weather Query" for temperature mode option.
2025-11-04 Cleanup and some improvements
    Prevent power output from going to 100% when booting in Automated controller mode with the temperature mode set to External Input. The External Input will stay at -127.0 until updated via the API. If temperature is -127.0 then power output will be set to the minimum output setting.
    Allow the AP mode SSID to be something other than CheapoDC. It will now match the hostname which is configurable in the WebUI.
    Javascript cleanup of CDCjs.js
    Documentation cleanup and typo fixes.
    [CDCSetup.cpp, CDCSetup.h, CDCdefines.h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]
2025-11-21 Add 3D files for SHT3x probe
    Add 3D files (STL, STEP, 3mf) for SHT3x support.
    [3-output-case.3mf, 3-output-switch-panel-sht3x.stl, 6-output-case.3mf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]
2026-06-13 V2.3.0 fixes (#20)
    * Update CDCSetup.cpp
    Need to check _humiditySensorStatus when setting Weather Source. Will prevent Internal Source from being available if the sensor is removed between reboots.
    * fix: wifi setup
    * fix: time wo network
    * Support ESP32 CA Cert Bundle for esp32FOTA
    Fix HTTPS authentication issue causing Web OTA Update to fail. Issue #19.
    * Update WebUI Copyright
    Update WebUI copyright to 2026
    * Documentation Updates
    Changes due to Web OTA Update issue preventing auto upgrade.
    * Documentation
    Additional documentation changes.
    * Prerelease cleanup
    Cleanup and restructure documentation.
    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
    [CDCSetup.cpp, CDCdefines.h, CDCesp32FOTA.cpp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]
